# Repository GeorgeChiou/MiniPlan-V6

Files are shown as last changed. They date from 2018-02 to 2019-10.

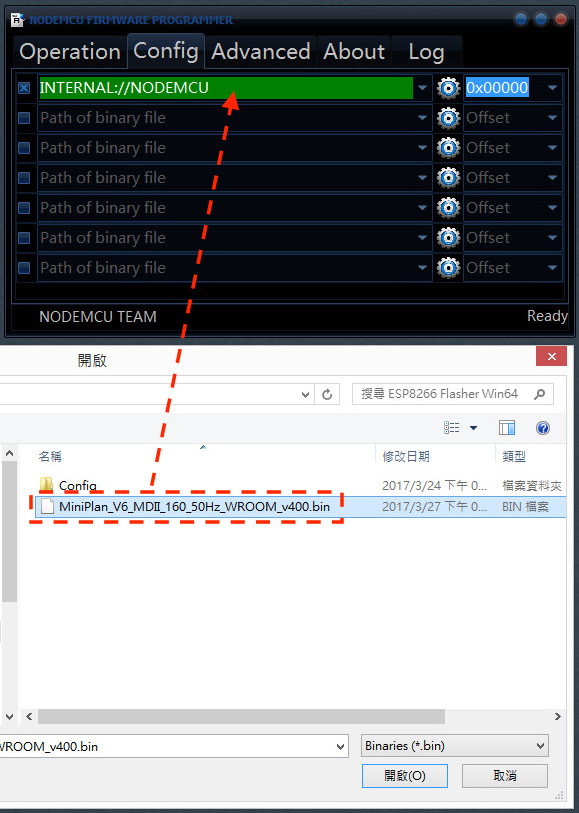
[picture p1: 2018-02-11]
ESP8266 Flasher Win32/Step3.jpg

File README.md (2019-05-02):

# MiniPlan V670 and Robot Power Package V320

MiniPlan V670 is an ideal piece of work for various types of projects when working with up to 20 Servo Motors.<br>

Specifications and Features<br>
Controls up to 20 servo motors (16PWM + 4 GPIO)<br>
Onboard USB to TTL so a regular USB to MicroUSB cable can be used to program the controller<br>
ESP-WROOM-02 directly from ESPRESSIF for faster, better, and stable connection<br>
4MB Flash memory<br>
Arduino IDE Compatible<br>
i2c connection port<br>
TTL connection port<br>
Dimensions L49mm X W43mm X H11.6mm<br>

Specifications of Robot Power Package V320<br>
8.4V/250mAh of power using 3 cells of Lithium Ion Capacitors<br>
Nominal output of 10C (2.5A) and maximum output of 15C (3.75A).<br>
Higher level safety using Lithium Ion Capacitors<br>
Dimensions L60mm X W43mm X H17.6mm<br>

MiniPlan Motion Editor :<br>
<br>

Assembly Instruction :<br>
<br>

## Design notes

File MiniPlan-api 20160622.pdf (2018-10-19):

1. 動作指定

帶入對應的參數即可做動作，但需要等做完後再執行下個動作

URL
{IP}/controller
變數名稱 | 傳遞方法 | 說明
pm | GET | 1: 向前走 2: 向後走 3: 向左走 4: 向右走 99: 停止
pms | GET | 1: Bow 2: Waving 3: Iron Man 4: Apache 5: Balance 6: Warm-Up

範例
http://192.168.4.1/controller?pm=1http://192.168.4.1/controller?pms=5

2. 裝置控制
直接指定 Servo 或 GPIO 的值

Servo Control
{IP}/controller
變數名稱 | 傳遞方法 | 說明
servo | GET | Servo 的編號
value | GET | 變化的數值

範例
http://192.168.4.1/controller?servo=5&value=20

GPIO Control
{IP}/controller
變數名稱 | 傳遞方法 | 說明
gpio | GET | GPIO 的編號
value | GET | 變化的數值

範例
http://192.168.4.1/controller?gpio=5&value=20

3. 參數設定
設定每個 Servo 校正數值

Setting Control
{IP}/save
變數名稱 | 傳遞方法 | 說明
key | GET | Servo 的編號
value | GET | 設定的數值

範例
http://192.168.4.1/save?key=5&value=20

4. 即時動作
傳入每個 Servo 動作矩陣數值

Online Control
{IP}/online
變數名稱 | 傳遞方法 | 說明
m0～m? | GET | Servo 的數值
t1 | GET | 設定執行時間的數值

範例
http://192.168.4.1/online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

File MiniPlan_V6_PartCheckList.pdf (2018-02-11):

Part No. | Print Settings | Qty.

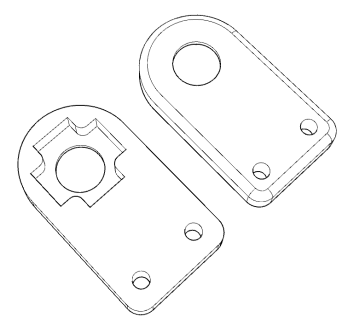
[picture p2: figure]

MiniPlan6_11 | Supports: No Resolution: 0.2mm Infill: 30% | □ 4

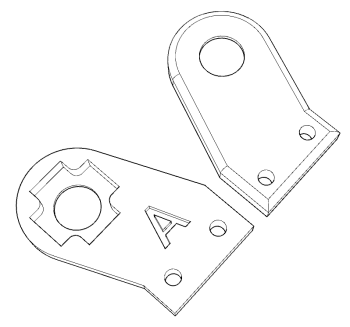
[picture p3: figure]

MiniPlan6_12A | Supports: No Resolution: 0.2mm Infill: 30% | □ 3

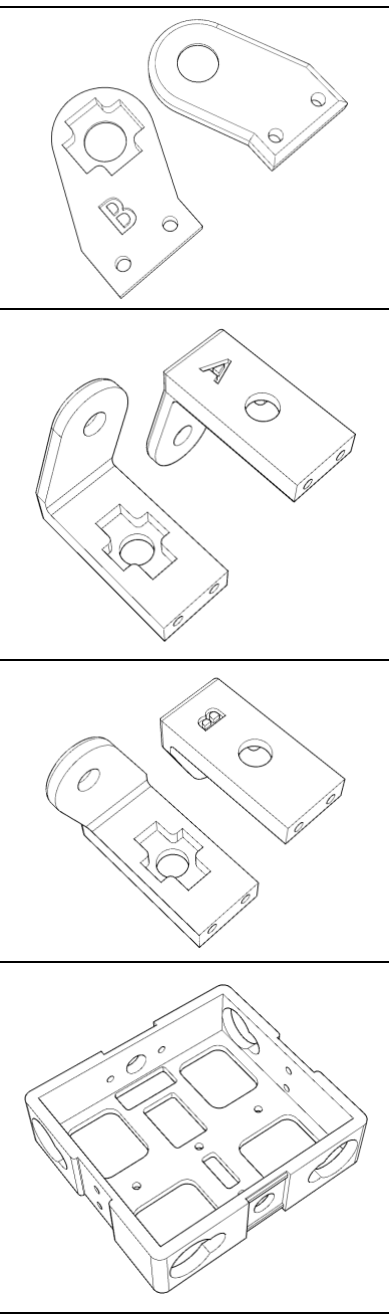
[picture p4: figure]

MiniPlan6_12B | Supports: No Resolution: 0.2mm Infill: 30% | □ 3
MiniPlan6_13A | Supports: No Resolution: 0.2mm Infill: 30% | □ 2
MiniPlan6_13B | Supports: No Resolution: 0.2mm Infill: 30% | □ 2
MiniPlan6_20 | Supports: No Resolution: 0.2mm Infill: 30% | □ 1

Part No. | Print Settings | Qty.

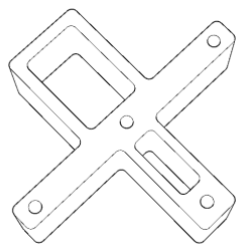
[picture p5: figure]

MiniPlan6_21 | Supports: No Resolution: 0.2mm Infill: 30% | □ 1
MiniPlan6_22B | Supports: No Resolution: 0.2mm Infill: 30% | □ 1

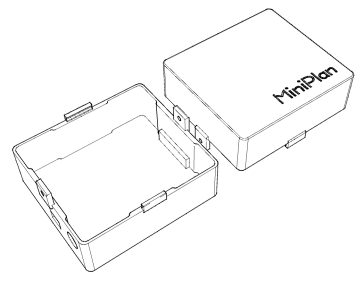
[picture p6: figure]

MiniPlan6_23B | Supports: No Resolution: 0.2mm Infill: 30% | □ 1

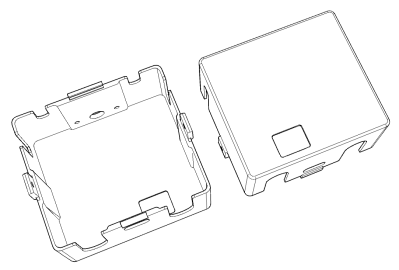
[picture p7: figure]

MiniPlan6_24B | Supports: No Resolution: 0.2mm Infill: 30% | □ 1

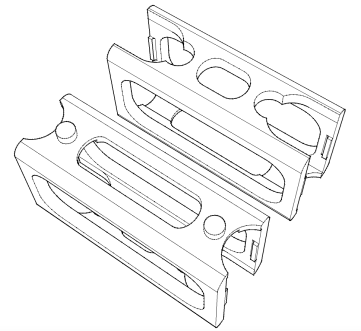
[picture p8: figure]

MiniPlan6_30 | Brim: Yes Supports: No Resolution: 0.2mm Infill: 30% | □ 2
MiniPlan6_31L | Supports: No Resolution: 0.2mm Infill: 20% | □ 1

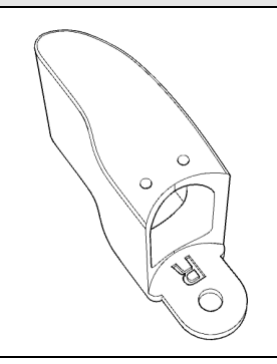
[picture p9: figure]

Part No. | Print Settings | Qty.
MiniPlan6_31R | Supports: No Resolution: 0.2mm Infill: 20% | □ 1

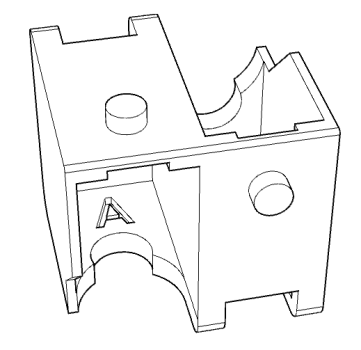
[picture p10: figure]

MiniPlan6_40A | Supports: Yes Resolution: 0.2mm Infill: 30% | □ 1

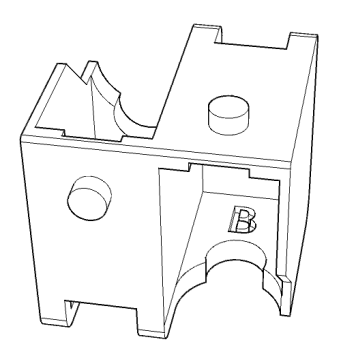
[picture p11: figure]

MiniPlan6_40B | Supports: Yes Resolution: 0.2mm Infill: 30% | □ 1

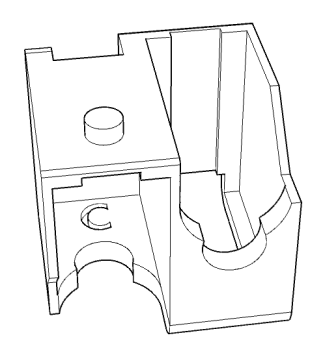
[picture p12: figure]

MiniPlan6_40C | Supports: Yes Resolution: 0.2mm Infill: 30% | □ 1
MiniPlan6_40D | Supports: Yes Resolution: 0.2mm Infill: 30% | □ 1

Part No. | Print Settings | Qty.

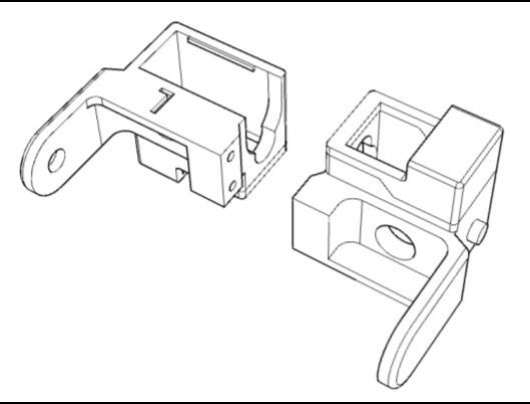
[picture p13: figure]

MiniPlan6_41L | Supports: No Resolution: 0.2mm Infill: 30% | □ 1

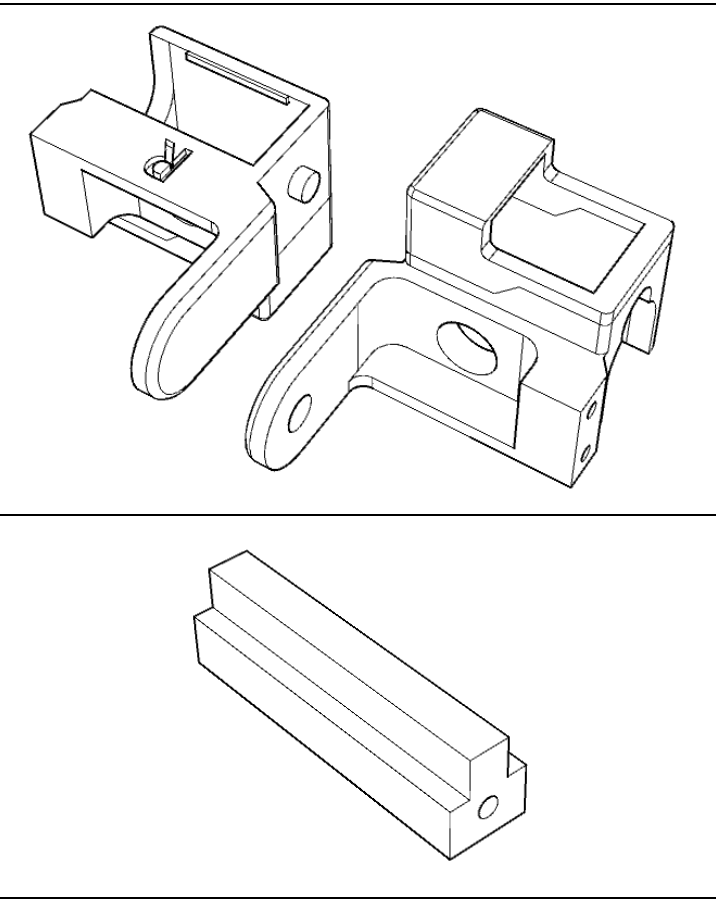
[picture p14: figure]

MiniPlan6_41R | Supports: No Resolution: 0.2mm Infill: 30% | □ 1
MiniPlan6_42 | Supports: No Resolution: 0.2mm Infill: 30% | □ 2

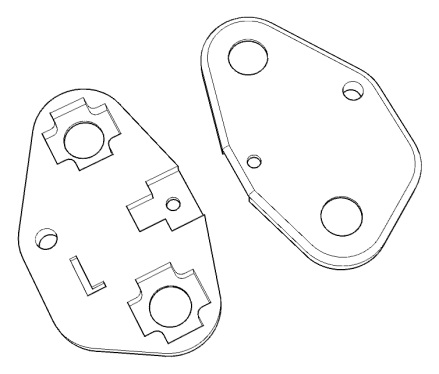
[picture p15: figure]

MiniPlan6_43L | Supports: No Resolution: 0.2mm Infill: 30% | □ 1

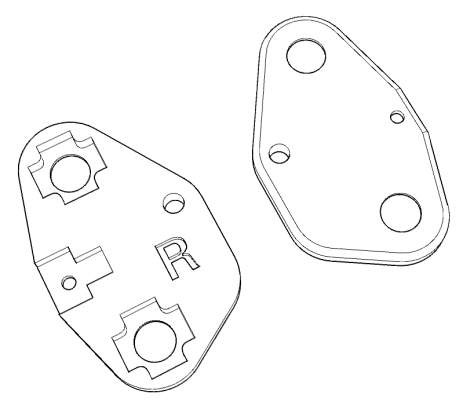
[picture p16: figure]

MiniPlan6_43R | Supports: No Resolution: 0.2mm Infill: 30% | □ 1

Part No. | Print Settings | Qty.

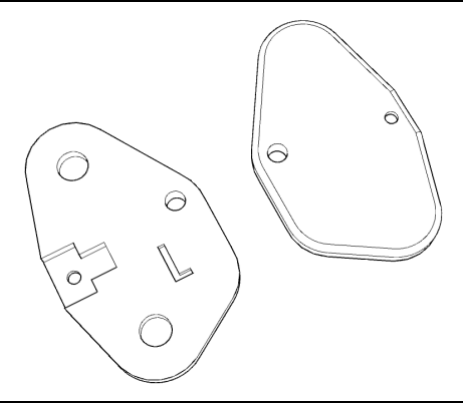
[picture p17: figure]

MiniPlan6_44L | Supports: No Resolution: 0.2mm Infill: 30% | □ 1
MiniPlan6_44R | Supports: No Resolution: 0.2mm Infill: 30% | □ 1
MiniPlan6_45L | Supports: No Resolution: 0.2mm Infill: 30% | □ 1
MiniPlan6_45R | Supports: No Resolution: 0.2mm Infill: 30% | □ 1

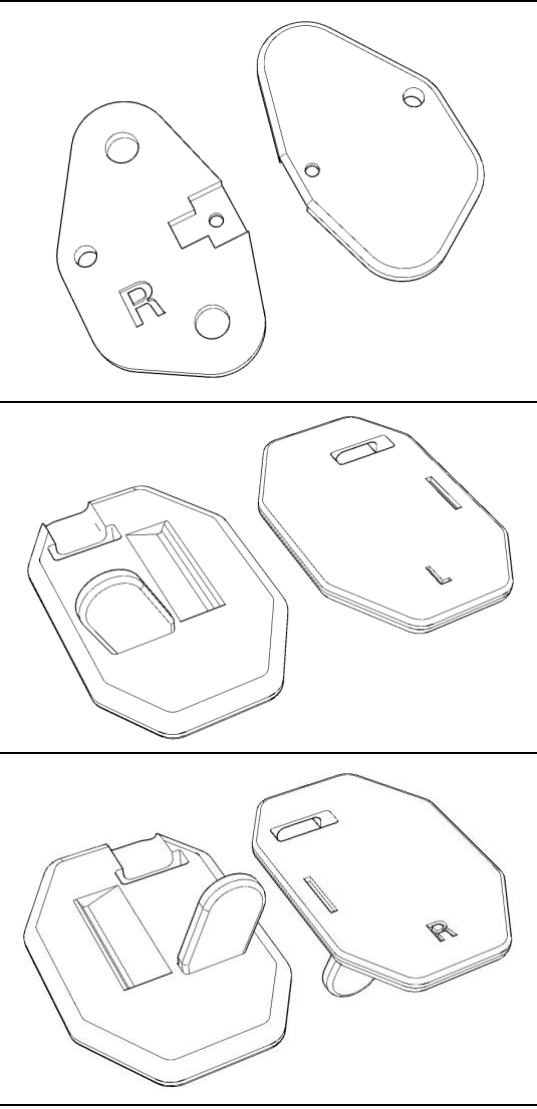
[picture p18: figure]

Print Check & Servo Cut Tool | Part No. | Print Settings | Qty.

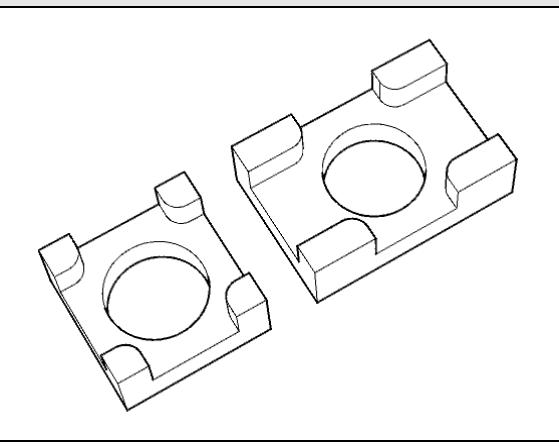
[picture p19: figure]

| MiniPlan6_70 | Supports: No Resolution: 0.2mm Infill: 100% | □ 1

Neck Mode 1 (Fix) | Part No. | Print Settings | Qty.
| MiniPlan6_50 | Supports: No Resolution: 0.2mm Infill: 100% | □ 1
Neck Mode 2 (Can Move) | Part No. | Print Settings | Qty.

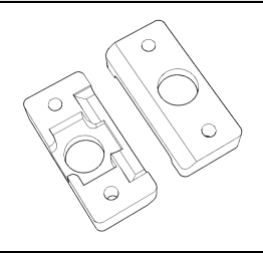
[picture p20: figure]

| MiniPlan6_51 | Supports: No Resolution: 0.2mm Infill: 100% | □ 1
| MiniPlan5_43 | Supports: No Resolution: 0.2mm Infill: 30% | □ 1

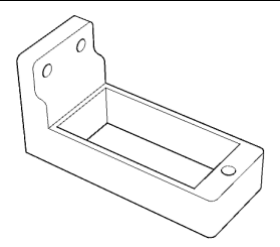
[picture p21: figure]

Skateboard | Part No. | Print Settings | Qty.

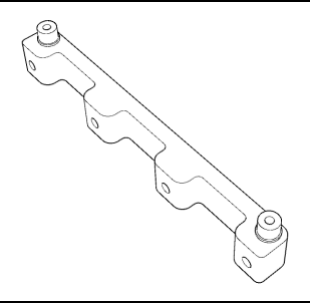
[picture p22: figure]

| MiniPlan6_60 | Supports: No Resolution: 0.2mm Infill: 30% | □ 4

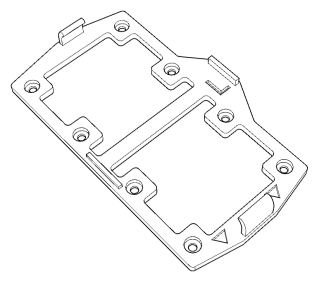
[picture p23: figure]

| MiniPlan6_61L | Supports: No Resolution: 0.2mm Infill: 100% | □ 1
| MiniPlan6_61R | Supports: No Resolution: 0.2mm Infill: 100% | □ 1

Head | Part No. | Print Settings | Qty.

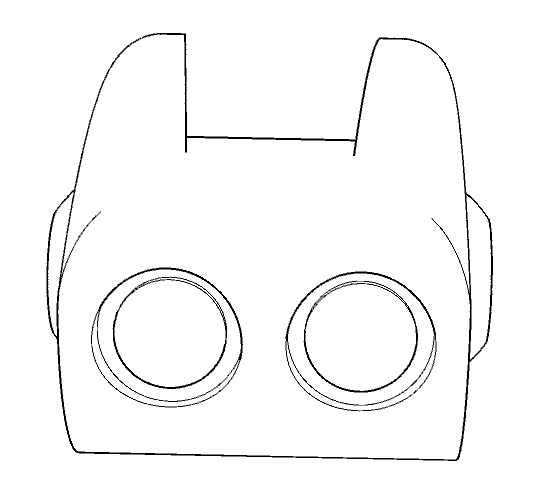
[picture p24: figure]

| MiniPlan5_40 Or MiniPlan5_40_chang | Rafts: Yes Supports: Yes Resolution: 0.2mm Infill: 20% | □ 1

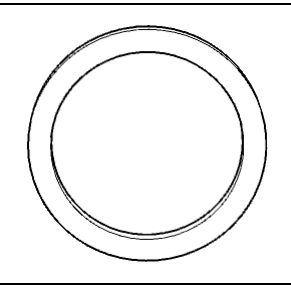
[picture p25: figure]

| MiniPlan51_70 | Supports: No Resolution: 0.2mm Infill: 100% | □ 2

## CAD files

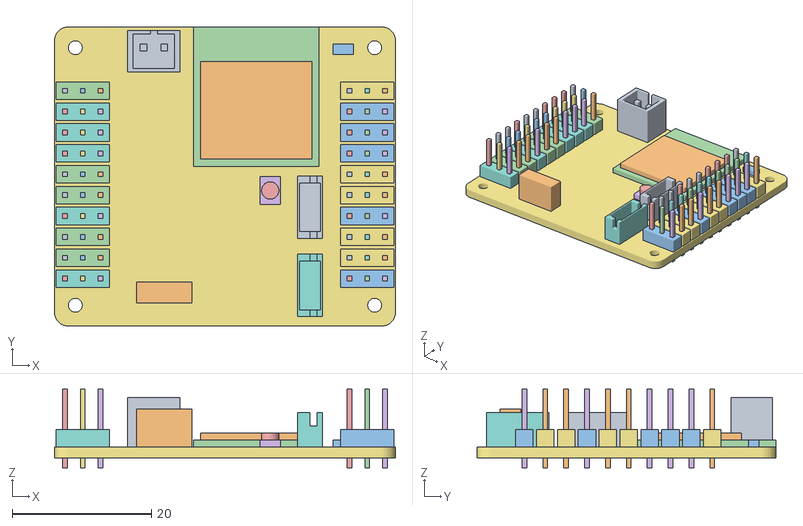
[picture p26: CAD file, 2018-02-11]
3D Mould Part/MiniPlan PCBA PIN v6.7.obj
49.0 x 43.0 x 11.3

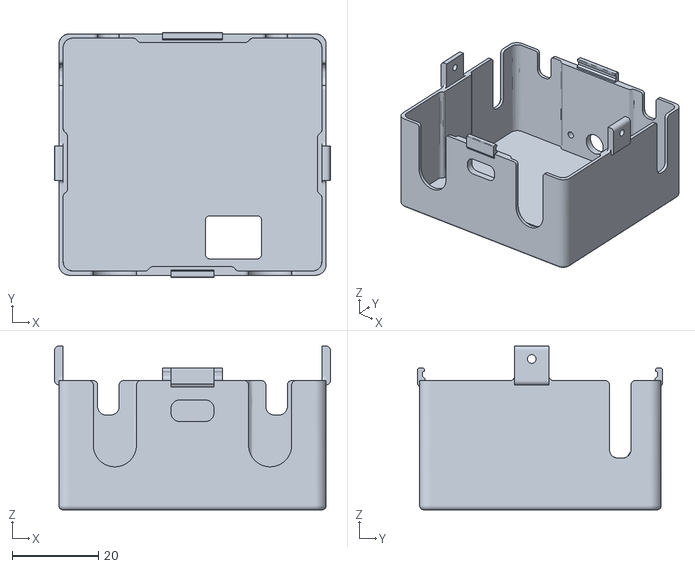
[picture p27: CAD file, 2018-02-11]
3D Mould Part/MiniPlan6_24B.stl
64.0 x 56.8 x 38.0

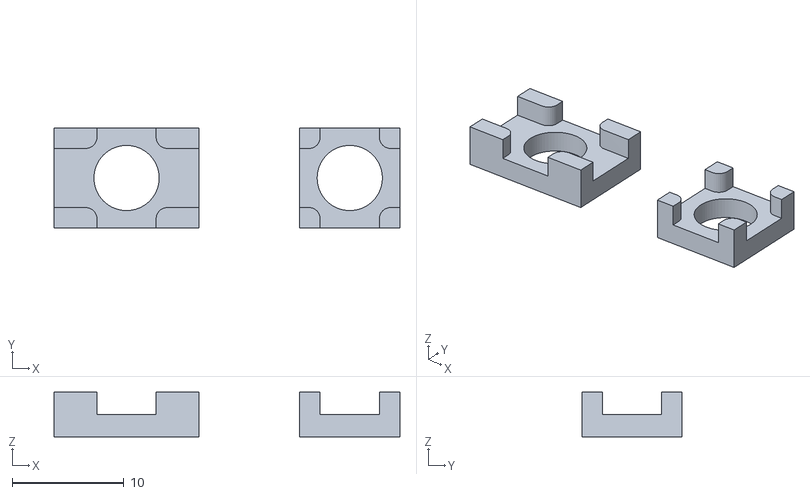
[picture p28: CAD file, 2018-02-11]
3D Mould Part/MiniPlan6_70.stl
31.0 x 9.00 x 4.00

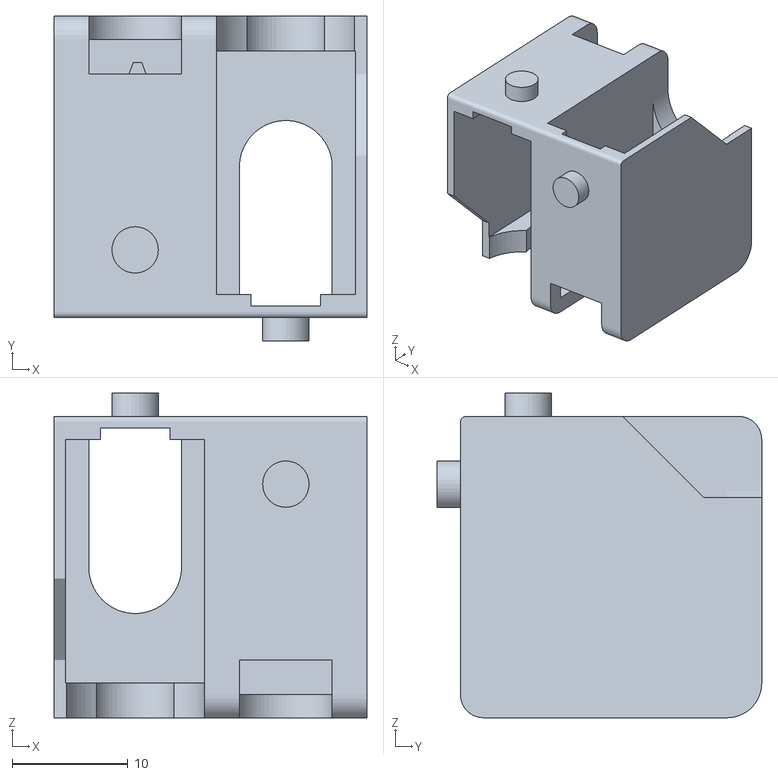
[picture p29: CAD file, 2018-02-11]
3D Mould Part/MiniPlan6_40A.stl
27.0 x 28.0 x 28.0

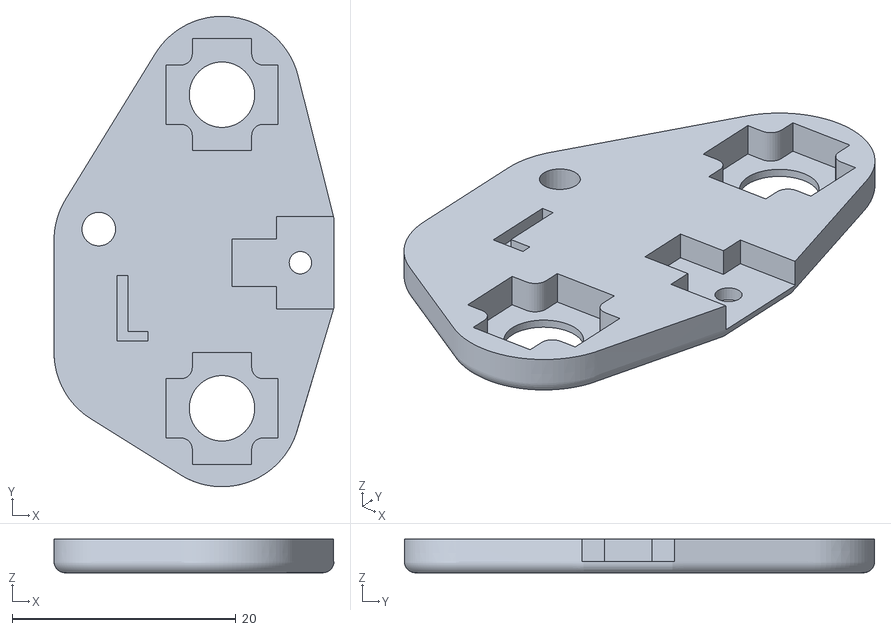
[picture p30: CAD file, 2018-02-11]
3D Mould Part/MiniPlan6_43L.stl
25.0 x 42.0 x 3.00

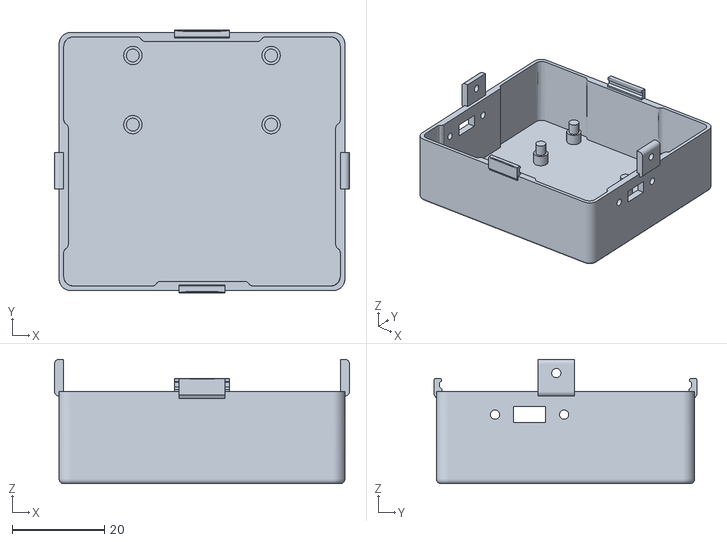
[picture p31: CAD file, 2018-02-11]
3D Mould Part/MiniPlan6_23A.stl
64.0 x 57.0 x 27.0

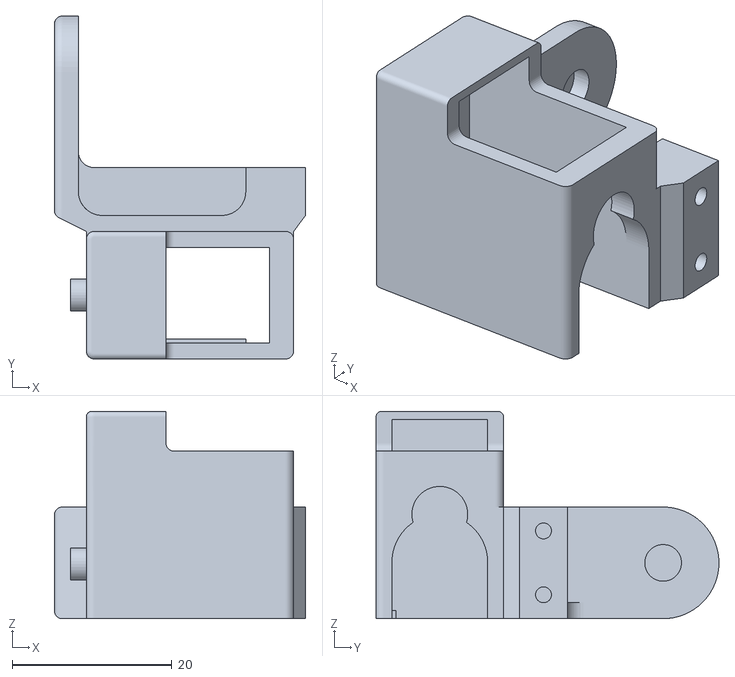
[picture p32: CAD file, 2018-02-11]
3D Mould Part/MiniPlan6_41L.stl
31.5 x 43.0 x 26.0

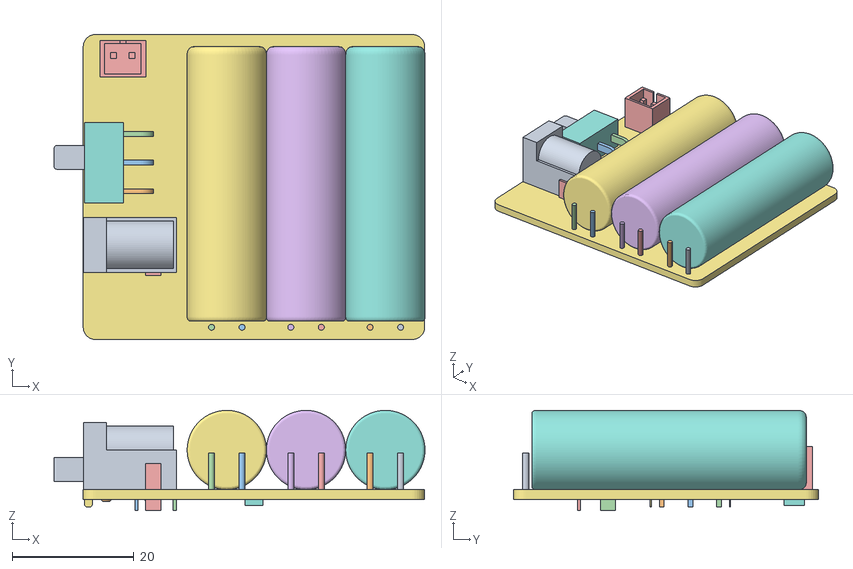
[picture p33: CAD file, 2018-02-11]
3D Mould Part/Robot Power Package V3.2 PCBA.obj
60.8 x 50.0 x 16.4

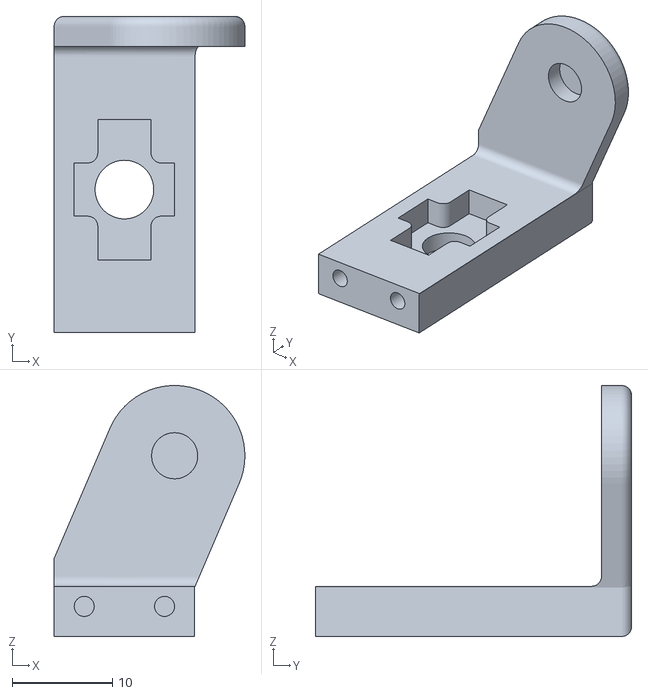
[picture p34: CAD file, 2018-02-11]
3D Mould Part/MiniPlan6_13A.stl
19.0 x 31.5 x 25.0

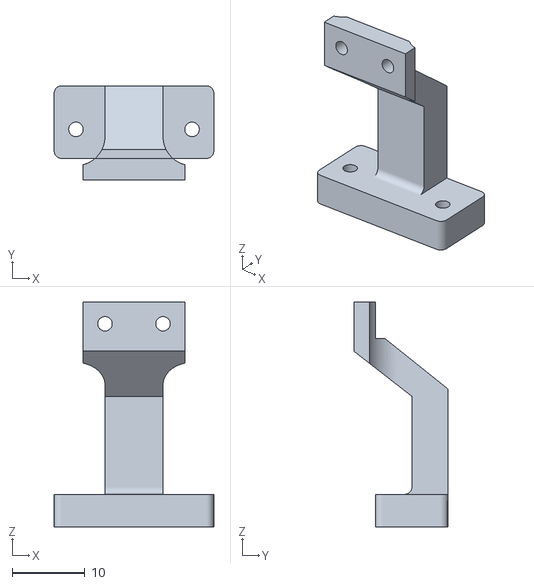
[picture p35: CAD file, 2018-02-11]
3D Mould Part/MiniPlan6_50.stl
22.0 x 13.0 x 31.0

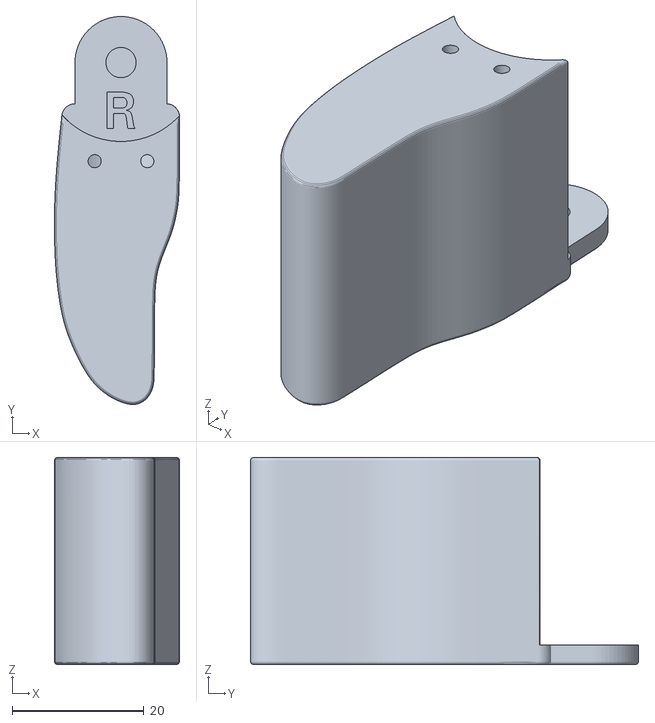
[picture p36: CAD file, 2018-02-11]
3D Mould Part/MiniPlan6_31R.stl
19.0 x 59.0 x 31.5

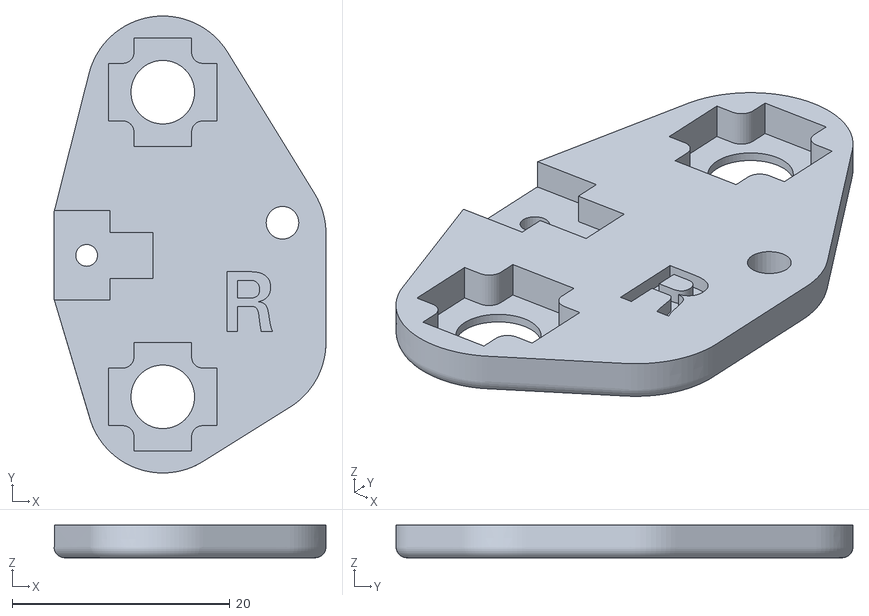
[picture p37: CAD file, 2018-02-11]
3D Mould Part/MiniPlan6_43R.stl
25.0 x 42.0 x 3.00

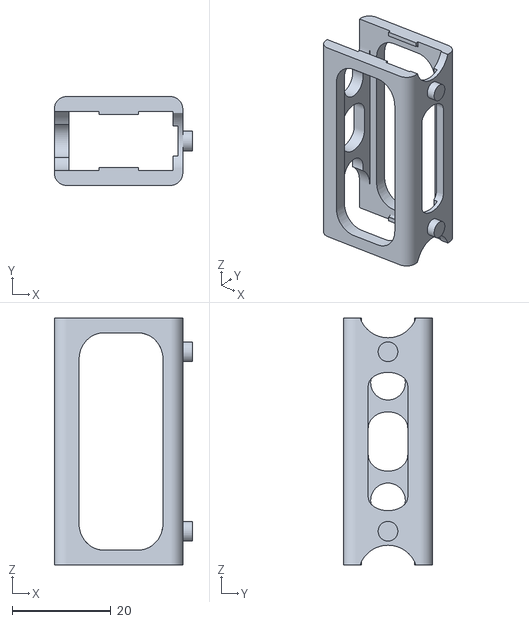
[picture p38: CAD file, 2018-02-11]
3D Mould Part/MiniPlan6_30.stl
28.0 x 18.0 x 50.0

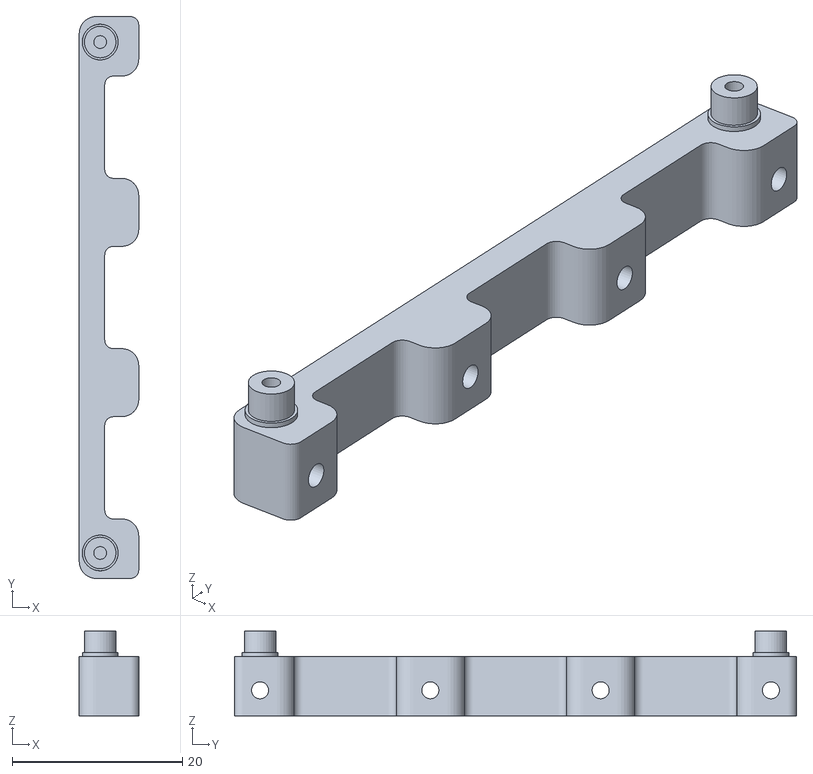
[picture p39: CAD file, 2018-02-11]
3D Mould Part/MiniPlan6_60.stl
7.00 x 66.0 x 9.95

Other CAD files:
3D Mould Part/MiniPlan6_40D.stl
3D Mould Part/MiniPlan6_44R.stl
3D Mould Part/MiniPlan6_40B.stl
3D Mould Part/MiniPlan6_12A.stl
3D Mould Part/MiniPlan51_70.stl
3D Mould Part/MiniPlan5_40.obj
3D Mould Part/MiniPlan5_43.stl
3D Mould Part/MiniPlan6_11.stl
3D Mould Part/MiniPlan6_12B.stl
3D Mould Part/MiniPlan6_13B.stl
3D Mould Part/MiniPlan6_20.stl
3D Mould Part/MiniPlan6_21.stl
3D Mould Part/MiniPlan6_22A.stl
3D Mould Part/MiniPlan6_22B.stl
3D Mould Part/MiniPlan6_23B.stl
3D Mould Part/MiniPlan6_23C.stl
3D Mould Part/MiniPlan6_23_MightyNet.stl
3D Mould Part/MiniPlan6_24A.stl
3D Mould Part/MiniPlan6_31L.stl
3D Mould Part/MiniPlan6_40C.stl
3D Mould Part/MiniPlan6_41R.stl
3D Mould Part/MiniPlan6_42.stl
3D Mould Part/MiniPlan6_44L.stl
3D Mould Part/MiniPlan6_45L.stl
3D Mould Part/MiniPlan6_45R.stl
3D Mould Part/MiniPlan6_51.stl
3D Mould Part/MiniPlan6_61L.stl
3D Mould Part/MiniPlan6_61R.stl

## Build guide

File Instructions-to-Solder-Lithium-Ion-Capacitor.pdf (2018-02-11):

## Instructions to Solder Lithium Ion Capacitor

Robot Power Pack V320

Due to international shipping regulations of Lithium Ion Batteries, although we are using Super Lithium Ion Capacitors on our product, in which classified as a high-volume Super Capacitor, to avoid issues with customs during exporting and importing, we've decided to leave the parts aside so the examiners don't misunderstood the product contained rechargeable batteries of Lithium Ion or NIMH etc..
Please follow the instructions below to properly install and solder these capacitors on to the Robot Power Pack V320 before enjoying the fun of our products!
1. Contents of received package,
1 x Robot Power Package V320 semi-populated board
3 x 2.4V Super Lithium Ion Capacitor (picture shows 250mAh version)

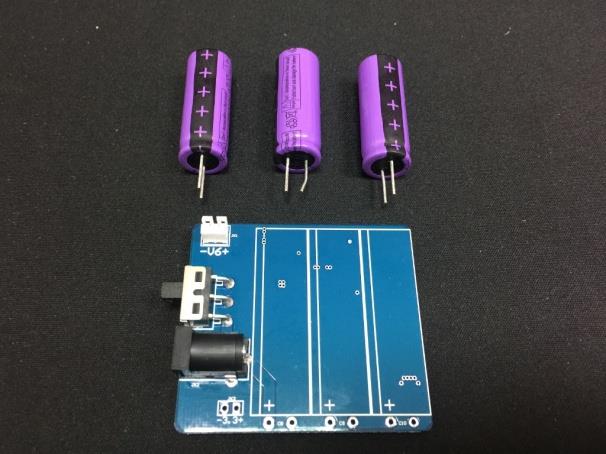
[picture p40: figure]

2. User fingers to bend the leads of capacitor as shown (bend both of them to the same direction). Note: Don't use conductive tools to bend the leads at the same time, shorting the two leads will cause instand discharge in which might damage your tools and the component.

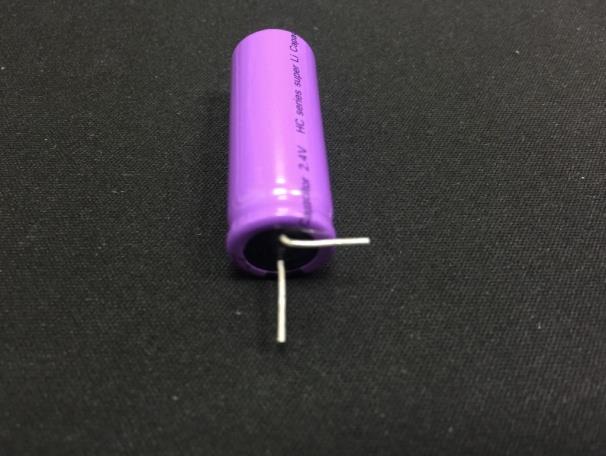
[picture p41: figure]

3. Insert the capacitor with the correct polarity.

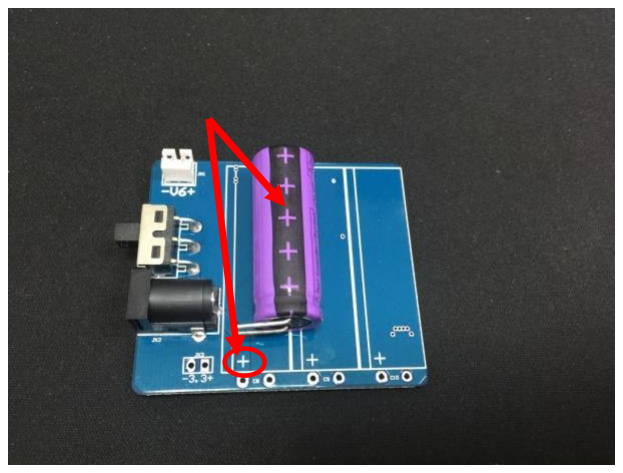
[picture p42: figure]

4. Insert the Capacitor onto the PCB as shown

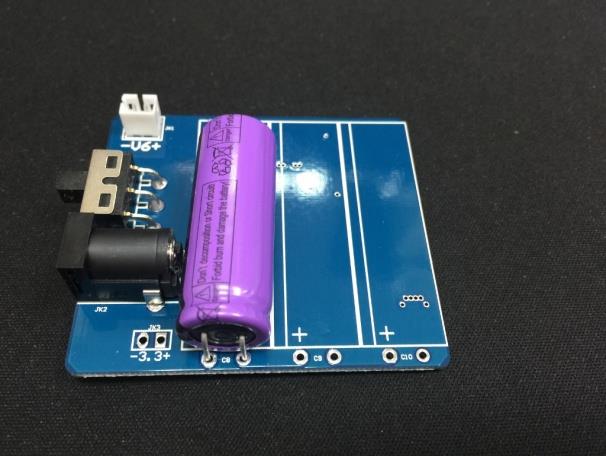
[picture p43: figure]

5. Solder the pins to PCB.
NOTE: Do not head the pins for too long in which may cause damage to components.

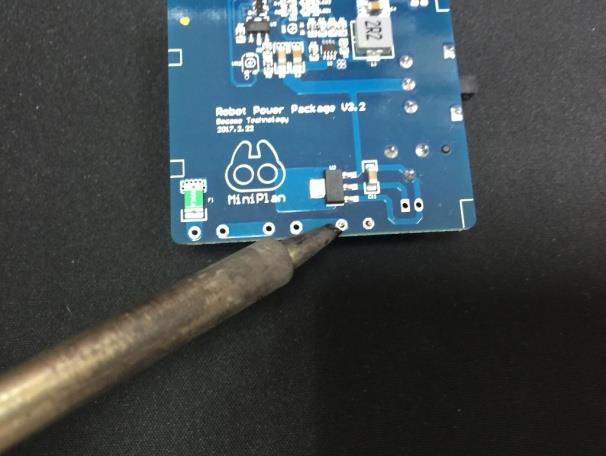
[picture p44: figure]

6. Repeat steps 1~5

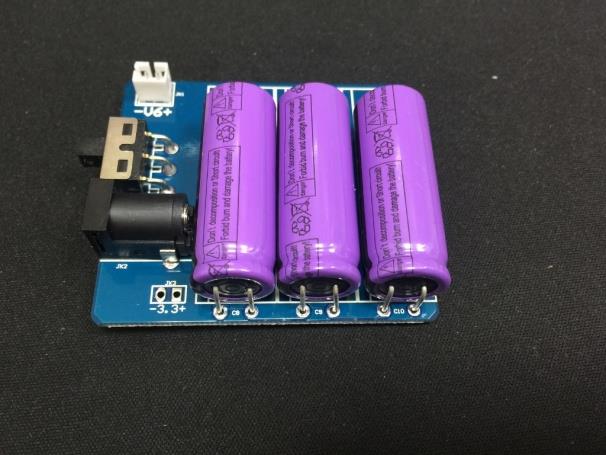
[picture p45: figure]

7. Apply adhesive between tips of capacitor and PCB to minimize movement.

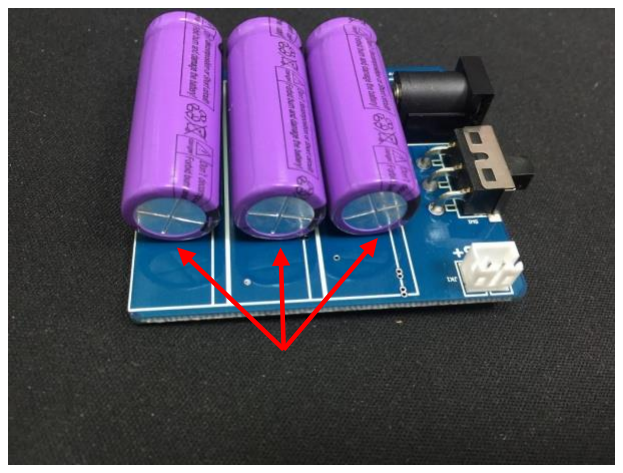
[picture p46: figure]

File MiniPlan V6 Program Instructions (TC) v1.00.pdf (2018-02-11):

# MiniPlan 編寫程式安裝說明

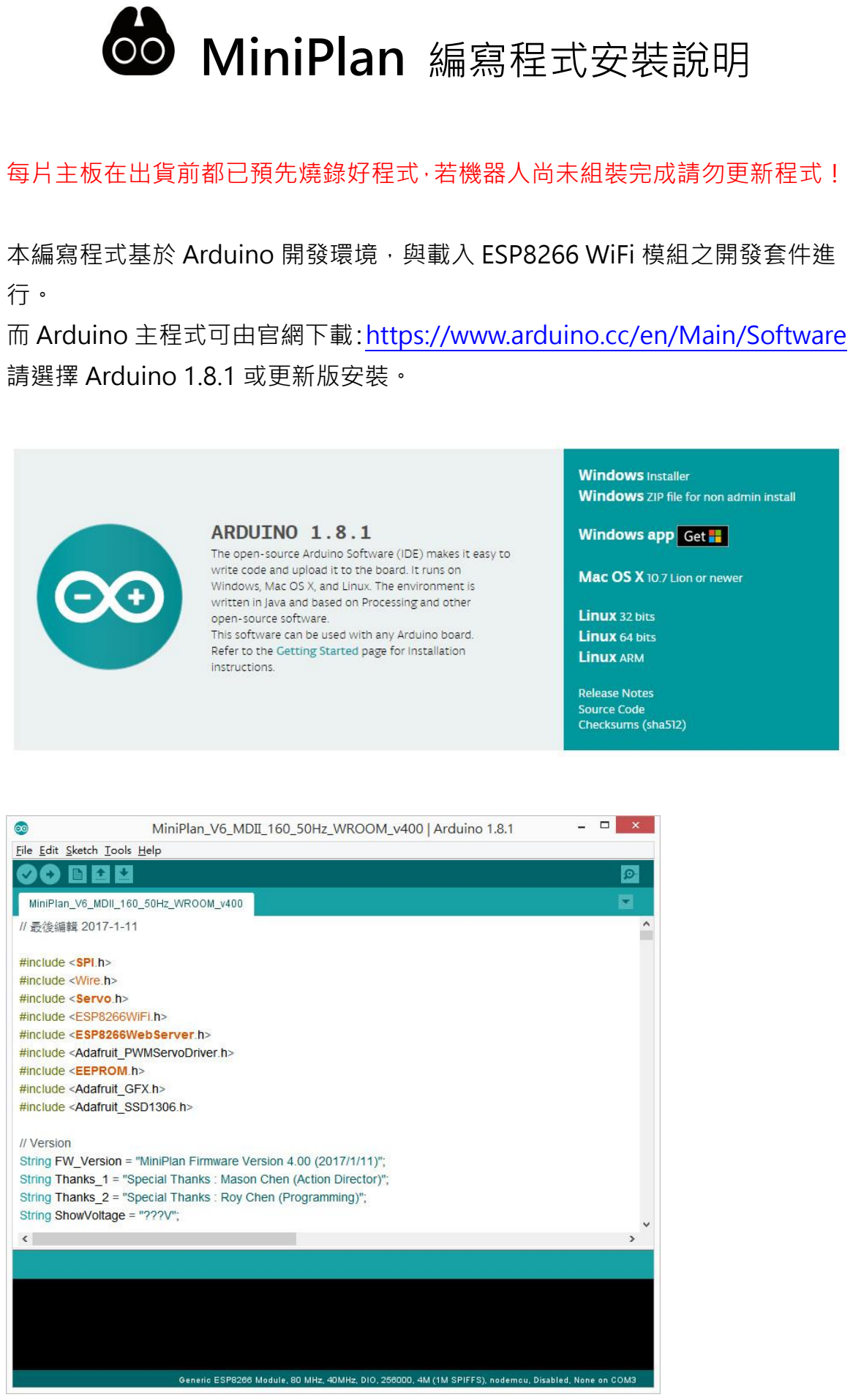
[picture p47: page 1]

每片主板在出貨前都已預先燒錄好程式，若機器人尚未組裝完成請勿更新程式！

本編寫程式基於 Arduino 開發環境，與載入 ESP8266 WiFi 模組之開發套件進 行。
而 Arduino 主程式可由官網下載：https://www.arduino.cc/en/Main/Software 請選擇 Arduino 1.8.1 或更新版安裝。

## 安裝檔案說明：

將下載 Zip 檔案接壓縮後，會有以下檔案。

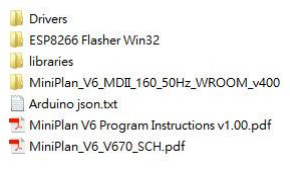
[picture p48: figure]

檔案夾 Drivers 為 USB 連線驅動程式。

檔案夾 ESP8266 Flasher Win32 為韌體燒錄重置或更新程式。

檔案夾 libraries 內的所有檔案
需拷貝到 My Documents\Arduino\Libraries\

檔案夾 MiniPlan_V6_MDII_160_50Hz_WROOM_v400 需拷貝到 My Documents\Arduino\

Arduino json.txt，下載 ESP8266 開發環境網站連結。

PDF 文件：
MiniPlan V6 Program Instructions v1.00.pdf，目前正在閱覽的文件。 MiniPlan_V6_V670_SCH.pdf，主控板電路圖。

## 安裝 ESP8266 WiFi 模組之開發套件：

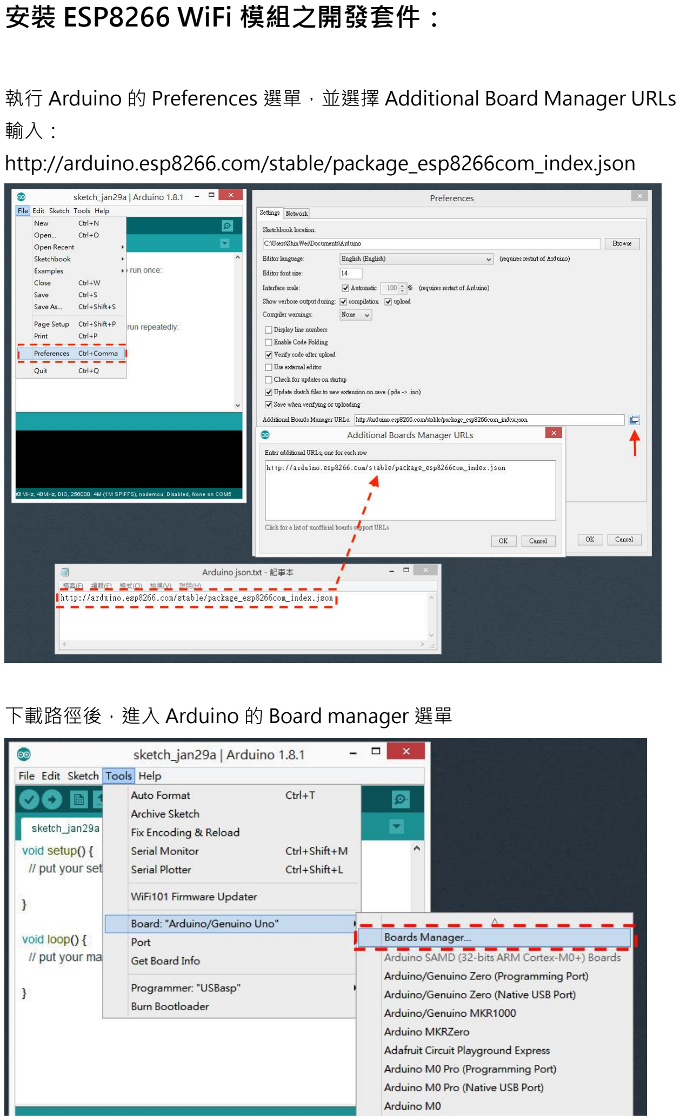
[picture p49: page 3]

執行 Arduino 的 Preferences 選單，並選擇 Additional Board Manager URLs 輸入：
http://arduino.esp8266.com/stable/package_esp8266com_index.json

下載路徑後，進入 Arduino 的 Board manager 選單

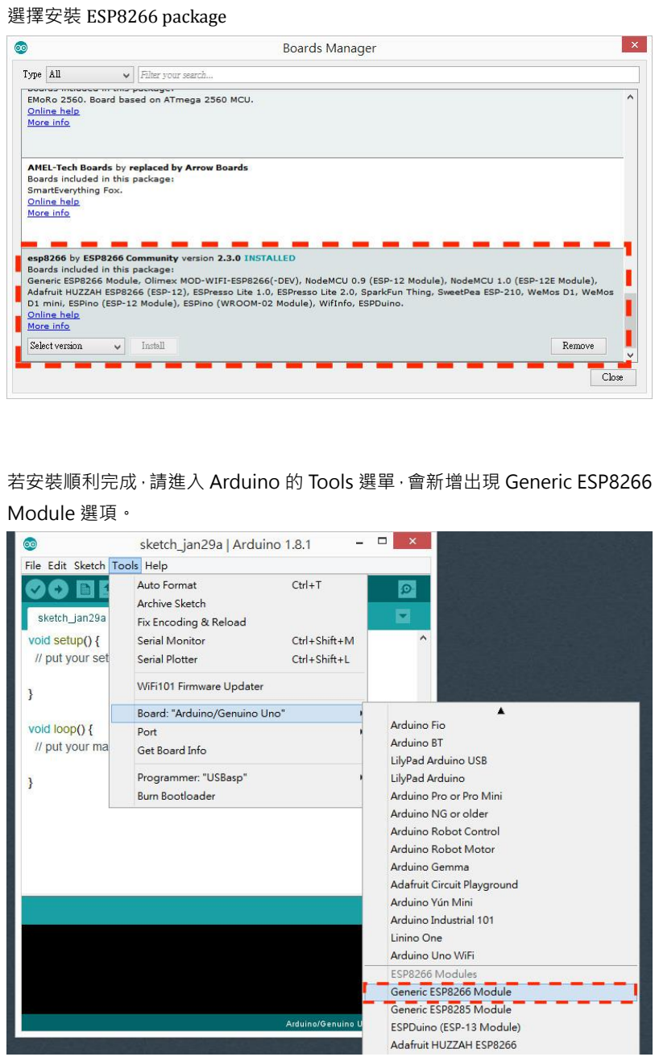
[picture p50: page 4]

選擇安裝 ESP8266 package

若安裝順利完成，請進入 Arduino 的 Tools 選單，會新增出現 Generic ESP8266 Module 選項。

請參照圖面上設定燒錄方式即可。

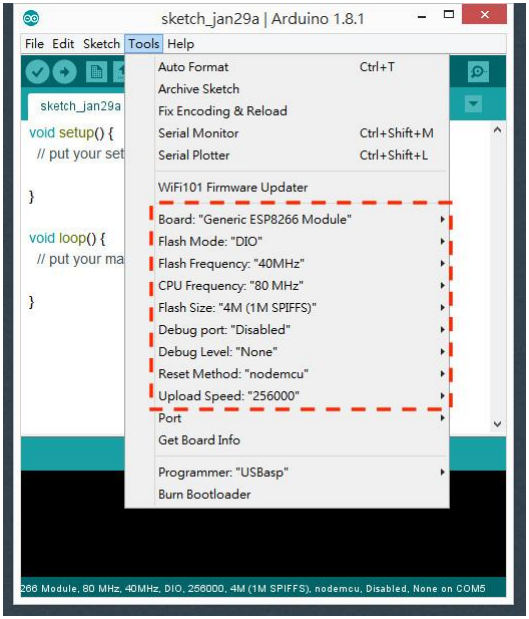
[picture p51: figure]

最後是安裝拷貝 Library。

一般來說都會在 Documents 目錄下找到！

再將解壓縮後的檔案夾 libraries 內的所有檔案拷貝進去即可。

## 安裝 PL2303TA USB to TTL 驅動程式：

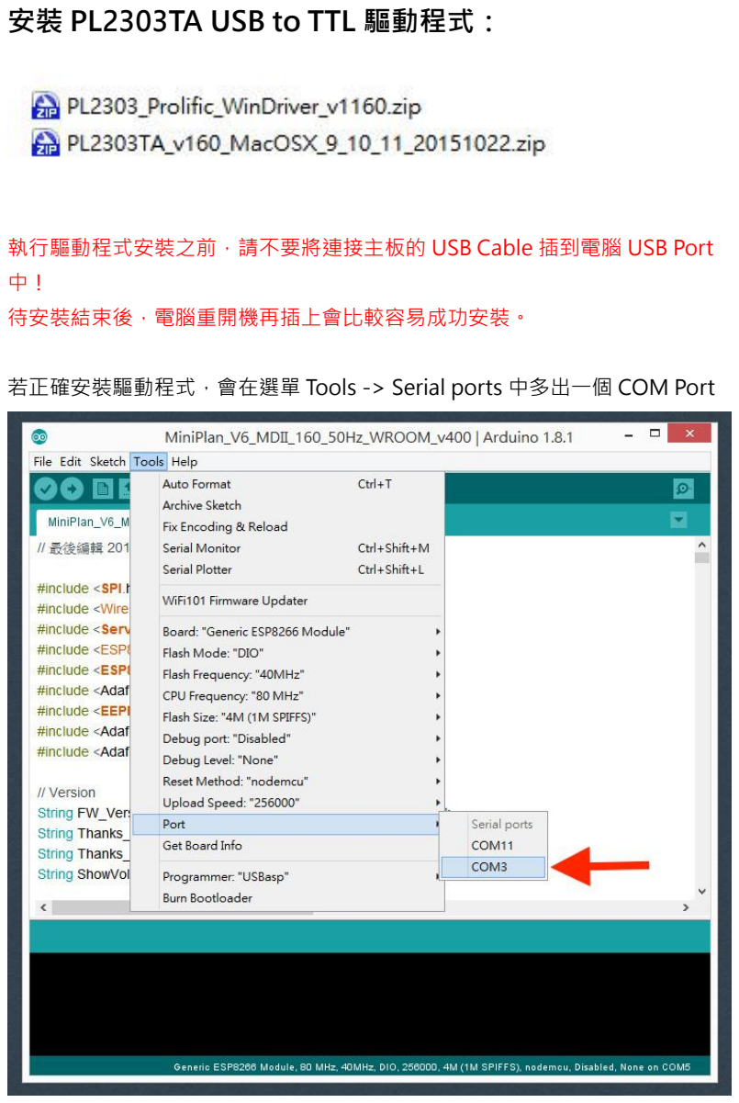
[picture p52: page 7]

執行驅動程式安裝之前，請不要將連接主板的 USB Cable 插到電腦 USB Port 中！
待安裝結束後，電腦重開機再插上會比較容易成功安裝。

若正確安裝驅動程式，會在選單 Tools -> Serial ports 中多出一個 COM Port

## 程式上傳硬體連接設置：

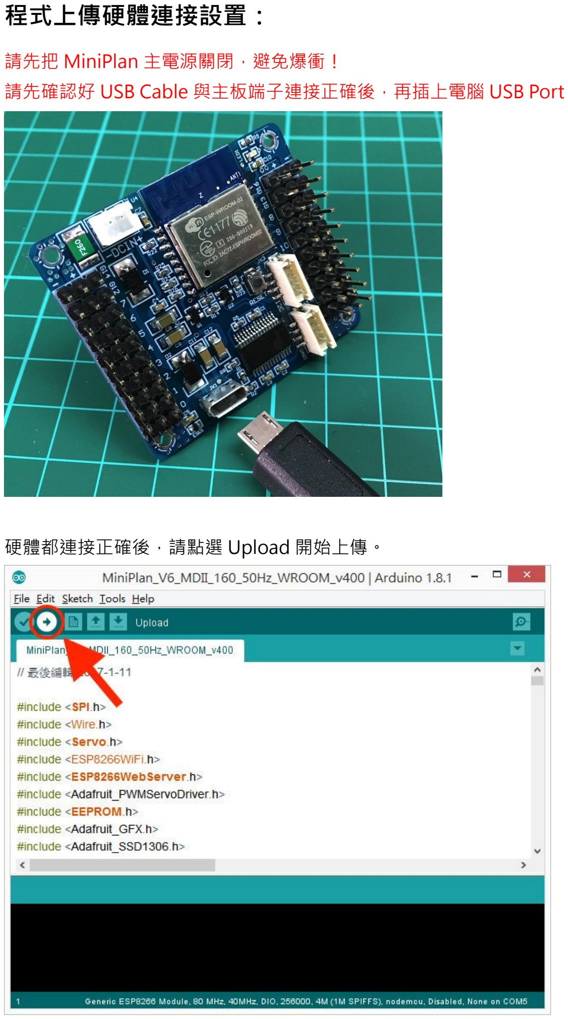
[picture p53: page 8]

請先把 MiniPlan 主電源關閉，避免爆衝！
請先確認好 USB Cable 與主板端子連接正確後，再插上電腦 USB Port

硬體都連接正確後，請點選 Upload 開始上傳。

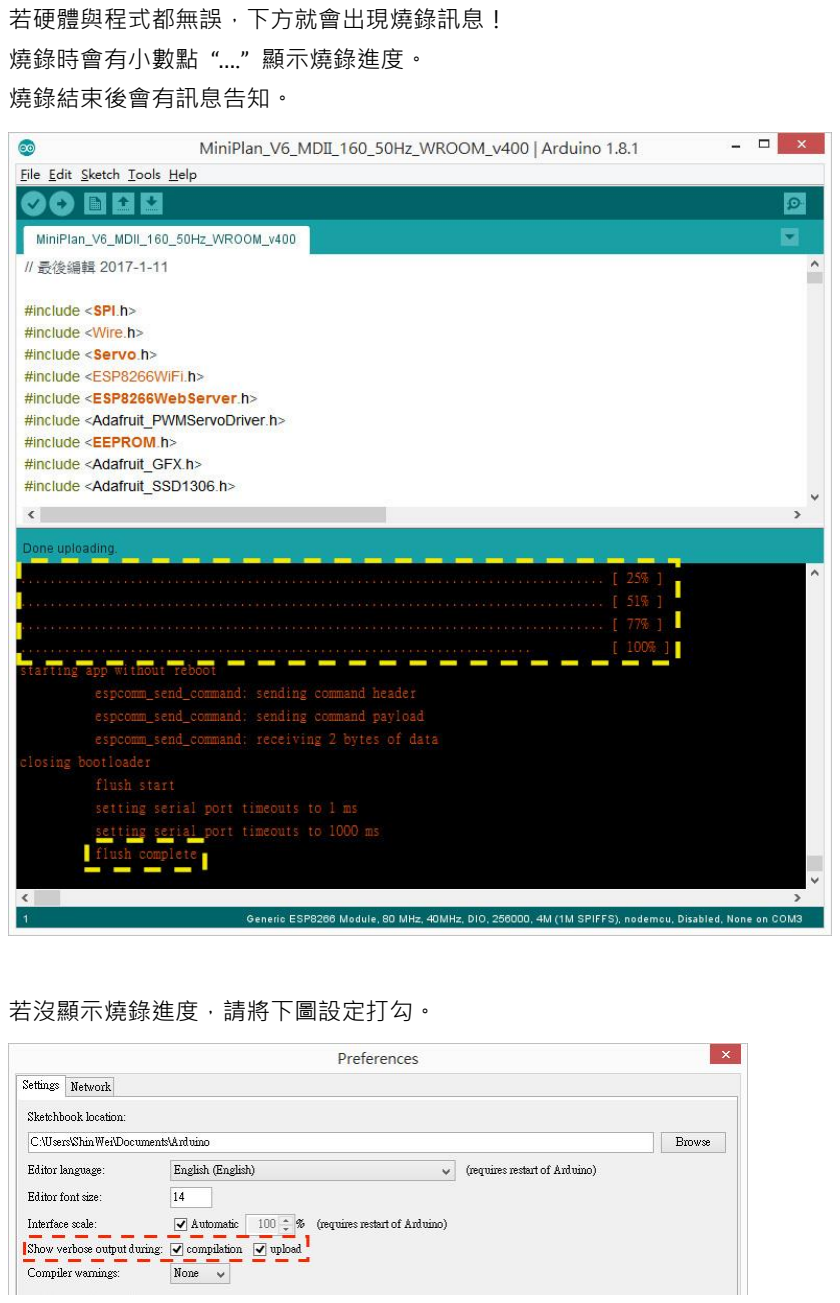
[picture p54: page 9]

若硬體與程式都無誤，下方就會出現燒錄訊息！
燒錄時會有小數點 “….” 顯示燒錄進度。
燒錄結束後會有訊息告知。

若沒顯示燒錄進度，請將下圖設定打勾。

## 發生錯誤情況：

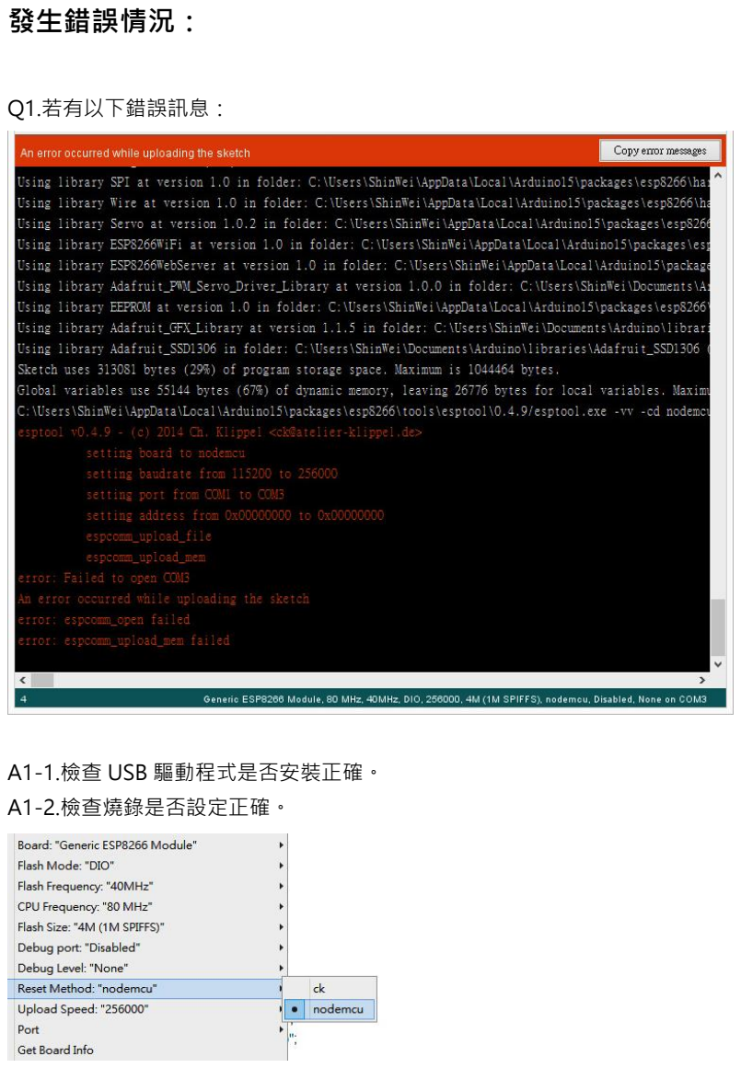
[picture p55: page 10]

Q1.若有以下錯誤訊息：

A1-1.檢查 USB 驅動程式是否安裝正確。
A1-2.檢查燒錄是否設定正確。

Q2.若有以下錯誤訊息：

A2.檢查檔案夾 libraries 內的所有檔案是否安裝正確。

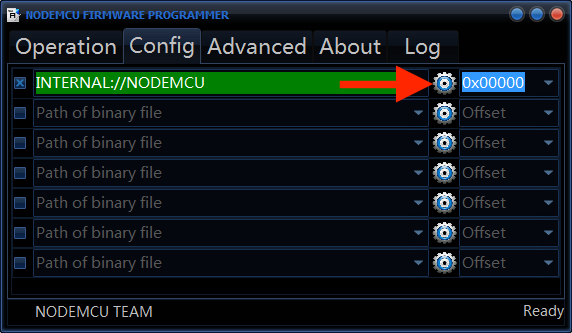
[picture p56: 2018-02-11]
ESP8266 Flasher Win32/Step2.jpg

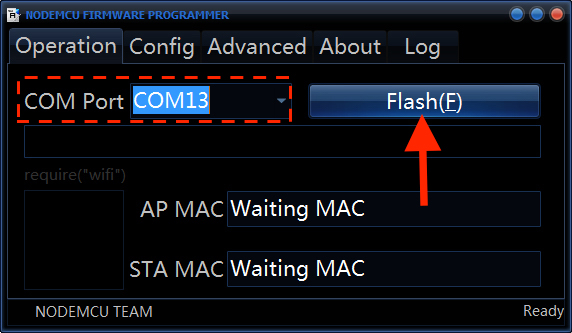
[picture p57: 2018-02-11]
ESP8266 Flasher Win32/Step4.jpg

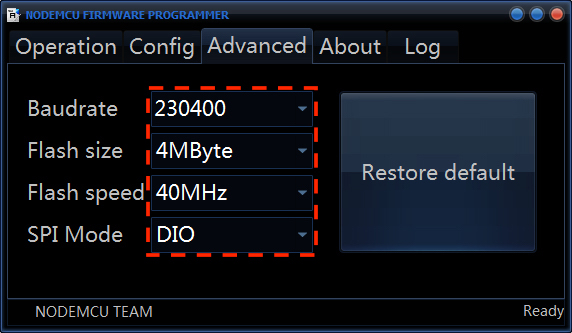
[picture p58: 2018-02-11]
ESP8266 Flasher Win32/Step1.jpg

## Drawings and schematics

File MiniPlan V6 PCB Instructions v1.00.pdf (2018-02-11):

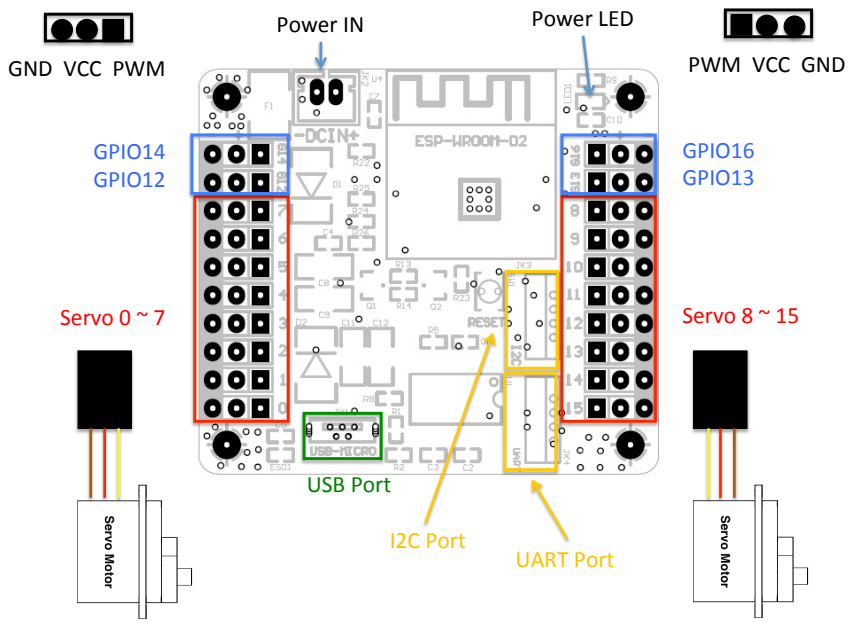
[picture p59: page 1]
Servo 0 ~ 7; Servo 8 ~ 15; GPIO16 GPIO13; GPIO14 GPIO12; USB Port; Power IN; GND VCC PWM; PWM VCC GND; I2C Port; UART Port; Power LED

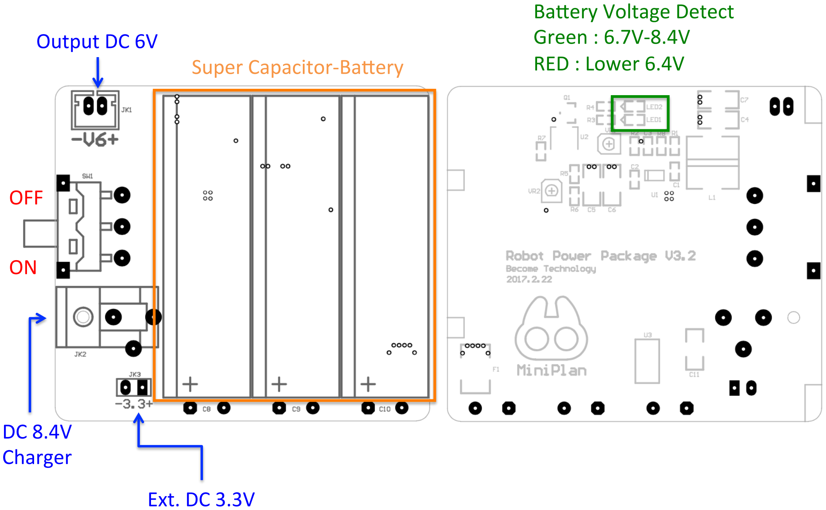
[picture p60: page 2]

OFF

ON

DC 8.4V
Charger
Ext. DC 3.3V

Output DC 6V

BaLery Voltage Detect
Green : 6.7V-8.4V
Super Capacitor-BaLery | RED : Lower 6.4V

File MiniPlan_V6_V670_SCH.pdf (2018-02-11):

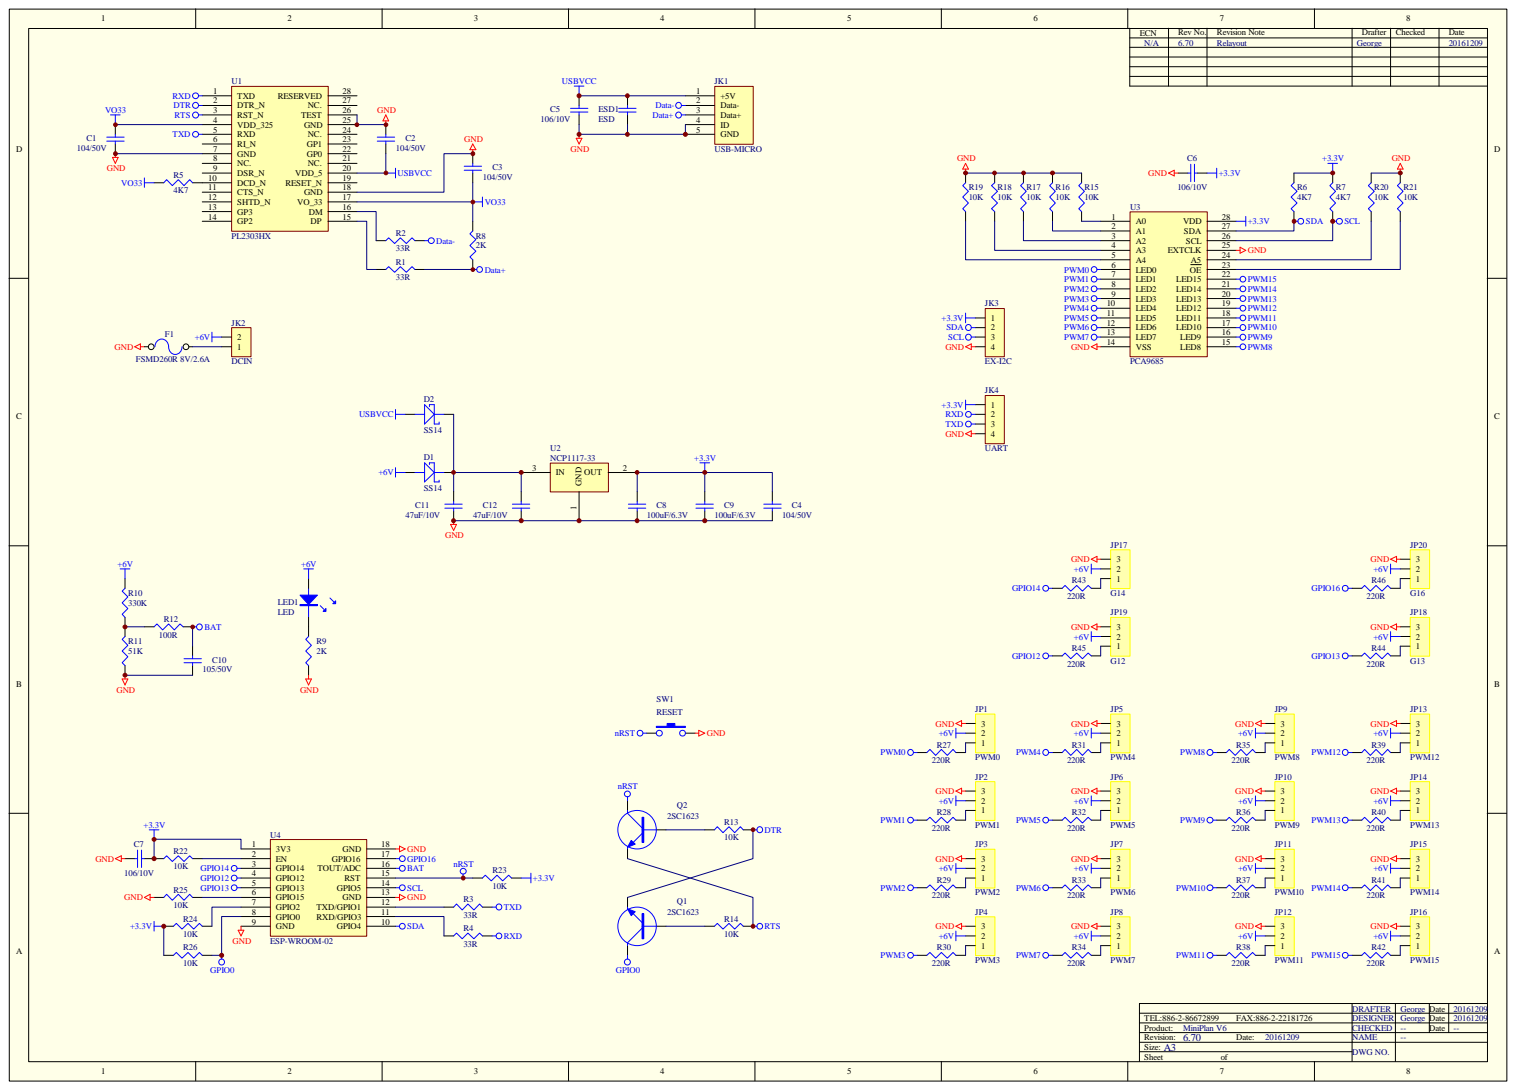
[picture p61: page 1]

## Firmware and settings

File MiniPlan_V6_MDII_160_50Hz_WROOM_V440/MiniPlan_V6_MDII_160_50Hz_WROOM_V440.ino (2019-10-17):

// 最後編輯 2017-3-23
// 初版

// 最後編輯 2017-5-14
// 修正 EEPROM.commit(); 與 EEPROM.h 衝突

// 最後編輯 2017-6-05
// 增加 handleGetEEPROM 傳輸 EEPROM 模式

// 最後編輯 2017-8-28
// 增加網頁對於 中文 支援指令

// 最後編輯 2019-10-17
// 因為 Adafruit_PWM_Servo_Driver_Library 版本問題，改由 Adafruit 正式版本網路下載
// PWM_Frequency = 50;


#include <SPI.h>
#include <Wire.h>
#include <Servo.h>
#include <ESP8266WiFi.h>
#include <ESP8266WebServer.h>
#include <Adafruit_PWMServoDriver.h>
#include <EEPROM.h>
#include <Adafruit_GFX.h>
#include <Adafruit_SSD1306.h>

// Version
String FW_Version = "MiniPlan Firmware Version 4.40 (2019/10/17)";
String Thanks_1 = "Special Thanks : Mason Chen (Action Director)";
String Thanks_2 = "Special Thanks : Roy Chen (Programming)";
String ShowVoltage = "???V";

//  I2C Address 0x3C
#define OLED_RESET LED_BUILTIN
Adafruit_SSD1306 display(-1);

// I2C Address 0x40
Adafruit_PWMServoDriver pwm = Adafruit_PWMServoDriver();

// Servos Matrix
const int ALLMATRIX = 21;    // 0 ~ 15 Servo + GPIO12 + GPIO13 + GPIO14 + GPIO16 + Run Time + Delay Time + PWM Frequency Calibration + Voltage Calibration
const int ALLSERVOS = 20;    // 0 ~ 15 Servo + GPIO12 + GPIO13 + GPIO14 + GPIO16

// ES08MDII Pulse Traveling 700us ~ 2300us 160度
const int PWM_Frequency = 50;    // PWM frequency 50Hz
const int PWMRES_Min = 1;        // PWM Resolution 1
const int PWMRES_Max = 160;      // PWM Resolution 160
const int SERVOMIN = 145;        // 145
const int SERVOMAX = 472;        // 472

// Servo Delay Base Time
const int BASEDELAYTIME = 10;    // 10ms

// AP Password
const char WiFiAPPSK[] = "12345678";

// Voltage Detected
const int Input_Voltage = 795;       // 約 6.00V
const int Input_MinVoltage = 590;    // 約 5.90V 啟動低壓機制
int Voltage_Conter;
int Voltage_Cab = 0;
int Input_Voltage_Low = 0;
int Voltage = Input_Voltage;
int Set_Voltage = Input_Voltage;

// Servo PWM Frequency
int Set_PWM_Freq = PWM_Frequency;

// Motion Data Index
int Servo_PROGRAM;
int Servo_PROGRAM_Stack;

// Servo ID
int GPIO_ID;
int GPIO12_PWM;
int GPIO13_PWM;
int GPIO14_PWM;
int GPIO16_PWM;

// Backup Servo Value
int Running_Servo_POS [ALLMATRIX];

// Engineering model
int Engineering_Model;

// OLED Display Index
int OLED_Display_Index = 0;

// Start Web Server
ESP8266WebServer server(80);

// Start GPIO Software Servo
Servo GPIO12SERVO;
Servo GPIO13SERVO;
Servo GPIO14SERVO;
Servo GPIO16SERVO;



/*============================================================================*/
// ES08MDII - 達文西姿勢
/////////////////////////////////////////////////////    0    ,    1    ,    2    ,    3    ,    4    ,    5    ,    6    ,    7    ,    8    ,    9    ,    10   ,    11   ,    12   ,    13   ,    14   ,    15   ,   G12   ,  G13   ,  G14   ,  G16   ,  ms
int Servo_Act_0 [ ] PROGMEM = {   60,      80,      50,     110,     50,     135,     50,      80,      80,     110,      25,      110,      50,      110,      80,      100,       90,       90,        90,        90,      0  };


/*============================================================================*/
// ES08MDII - 立正
/////////////////////////////////////////////////////    0    ,    1    ,    2    ,    3    ,    4    ,    5    ,    6    ,    7    ,    8    ,    9    ,    10   ,    11   ,    12   ,    13   ,    14   ,    15   ,   G12   ,  G13   ,  G14   ,  G16   ,  ms
int Servo_Act_1 [ ] PROGMEM = {   60,      80,      50,     110,     50,     135,    125,     80,      80,      35,       25,      110,      50,      110,      80,      100,       90,       90,        90,        90,      0  };


/*============================================================================*/
// 鞠躬動作
int Servo_Prg_31_Step = 4;
int Servo_Prg_31 [][ALLMATRIX] PROGMEM = {
  //   0    ,    1    ,    2    ,    3    ,    4    ,    5    ,    6    ,    7    ,    8    ,    9    ,    10   ,    11   ,    12   ,    13   ,    14   ,    15   ,   G12   ,  G13   ,  G14   ,  G16   ,  ms
  {   60,      80,      50,     110,     50,     155,    115,     40,     140,     35,      105,     110,      50,      110,      80,      100,      90,        90,        90,       90,       500   },
  {   60,      65,      50,      60,      50,     155,    115,     40,     140,     35,      105,     110,      97,      110,      95,      100,      90,        90,        90,       90,       500   },
  {   60,      65,      50,      60,      50,     155,    115,     40,     140,     35,      105,     110,      97,      110,      95,      100,      90,        90,        90,       90,       1000 },
  {   60,      80,      50,     110,     50,     135,    125,     80,      80,      35,       25,      110,      50,      110,      80,      100,      90,        90,        90,       90,       800   }   // 立正
};


/*============================================================================*/
// 揮手動作
int Servo_Prg_32_Step = 9;
int Servo_Prg_32 [][ALLMATRIX] PROGMEM = {
  //   0    ,    1    ,    2    ,    3    ,    4    ,    5    ,    6    ,    7    ,    8    ,    9    ,    10   ,    11   ,    12   ,    13   ,    14   ,    15   ,   G12   ,  G13   ,  G14   ,  G16   ,  ms
  {   60,      80,      50,     110,     50,     135,    125,     80,      60,      75,      125,     110,      50,      110,      80,      100,      90,        60,        90,        90,      500  },
  {   60,      80,      50,     110,     50,     135,    125,     80,      80,      35,      125,     110,      50,      110,      80,      100,      90,        60,        90,        90,      300  },
  {   60,      80,      50,     110,     50,     135,    125,     80,      60,      75,      125,     110,      50,      110,      80,      100,      90,        60,        90,        90,      300  },
  {   60,      80,      50,     110,     50,     135,    125,     80,      80,      35,      125,     110,      50,      110,      80,      100,      90,        60,        90,        90,      300  },

  {   60,      80,      50,     110,     50,      35,      85,     100,     80,      35,       30,      110,      50,      110,      80,      100,      90,       120,       90,        90,      500  },
  {   60,      80,      50,     110,     50,      35,     115,     80,      80,      35,       30,      110,      50,      110,      80,      100,      90,       120,       90,        90,      300  },
  {   60,      80,      50,     110,     50,      35,      85,     100,     80,      35,       30,      110,      50,      110,      80,      100,      90,       120,       90,        90,      300  },
  {   60,      80,      50,     110,     50,      35,     115,     80,      80,      35,       30,      110,      50,      110,      80,      100,      90,       120,       90,        90,      300  },

  {   60,      80,      50,     110,     50,     135,    125,     80,      80,      35,       25,      110,      50,      110,      80,      100,      90,        90,        90,        90,      800  }   // 立正
};


/*============================================================================*/
// 鋼鐵人動作
int Servo_Prg_33_Step = 8;
int Servo_Prg_33 [][ALLMATRIX] PROGMEM = {
  //   0    ,    1    ,    2    ,    3    ,    4    ,    5    ,    6    ,    7    ,    8    ,    9    ,    10   ,    11   ,    12   ,    13   ,    14   ,    15   ,   G12   ,  G13   ,  G14   ,  G16   ,  ms
  {   50,      80,      50,     110,     45,     155,    105,    120,     40,     105,      25,      100,      50,      110,      80,       90,       90,        60,        90,        90,      300  },
  {   50,      80,      50,     110,     45,     155,    105,    120,     40,     105,      25,      100,      50,      110,      80,       90,       90,        60,        90,        90,      800  },

  {   70,      80,      50,     110,     60,     135,     55,     120,     40,      55,        5,       115,      50,      110,      80,      110,      90,       120,       90,        90,      300  },
  {   70,      80,      50,     110,     60,     135,     55,     120,     40,      55,        5,       115,      50,      110,      80,      110,      90,       120,       90,        90,      800  },

  {   60,      80,      50,     110,     50,      55,     105,    120,     40,      55,      105,     110,      50,      110,      80,      100,      90,        90,        90,        90,      500  },
  {   60,      65,      50,      95,      50,      55,     140,    120,     40,      15,      105,     110,      65,      110,      94,      100,      90,        90,        90,        90,      500  },

  {   60,      65,      50,      95,      50,      55,     140,    120,     40,      15,      105,     110,      65,      110,      94,      100,      90,        90,        90,        90,      800  },
  {   60,      80,      50,     110,     50,     135,    125,     80,      80,      35,       25,      110,      50,      110,      80,      100,      90,        90,        90,        90,      800  }   // 立正
};


/*============================================================================*/
// 右邊單腳側傾動作
int Servo_Prg_34_Step = 7;
int Servo_Prg_34 [][ALLMATRIX] PROGMEM = {
  //   0    ,    1    ,    2    ,    3    ,    4    ,    5    ,    6    ,    7    ,    8    ,    9    ,    10   ,    11   ,    12   ,    13   ,    14   ,    15   ,   G12   ,  G13   ,  G14   ,  G16   ,  ms
  {   70,      80,      50,     110,     60,     135,    105,     35,      80,      85,       25,      115,      50,      110,      80,      110,      90,        90,        90,        90,      500  },
  {   70,      80,      50,     110,     60,     135,    105,     35,      80,      85,       25,      115,      50,      110,      80,      115,      90,        90,        90,        90,      300  },
  {   70,      80,      50,     110,     60,     135,    105,     35,     140,     15,      105,     100,      50,      110,      80,      120,      90,        90,        90,        90,      500  },
  {   70,      80,      50,     110,     60,     135,    105,     35,     140,     15,      105,     100,      50,      110,      80,      120,      90,       120,       90,        90,      800  },
  {   70,      80,      50,     110,     60,     135,    105,     35,      80,      85,       25,      115,      50,      110,      80,      115,      90,       120,       90,        90,      600  },
  {   70,      80,      50,     110,     60,     135,    105,     35,      80,      85,       25,      115,      50,      110,      80,      110,      90,        90,        90,        90,      500  },
  {   60,      80,      50,     110,     50,     135,    125,     80,      80,      35,       25,      110,      50,      110,      80,      100,      90,        90,        90,        90,      800  }   // 立正
};


/*============================================================================*/
// 左邊單腳平衡動作
int Servo_Prg_35_Step = 12;
int Servo_Prg_35 [][ALLMATRIX] PROGMEM = {
  //   0    ,    1    ,    2    ,    3    ,    4    ,    5    ,    6    ,    7    ,    8    ,    9    ,    10   ,    11   ,    12   ,    13   ,    14   ,    15   ,   G12   ,  G13   ,  G14   ,  G16   ,  ms
  {   50,      80,      50,     110,     45,     135,     50,      80,      80,     110,      25,      100,      50,      110,      80,       90,       90,        90,        90,        90,      500  },
  {   50,      80,      50,     110,     45,      85,      50,      80,      80,     110,      75,      100,      50,      110,      85,       90,       90,        90,        90,        90,      300  },
  {   45,      80,      50,     110,     60,      85,      50,      80,      80,     110,      75,      100,      50,      110,      85,       90,       90,        90,        90,        90,      500  },
  {   45,      80,      50,     110,     60,      85,      50,      80,      80,     110,      75,      100,      50,      110,      85,       90,       90,        90,        90,        90,      600  },

  {   45,      60,      50,      50,      60,      85,      50,      80,      80,     110,      75,      100,      50,      110,      85,       90,       90,        90,        90,        90,      900  },
  {   45,      60,      50,      50,      60,      85,      30,      80,      80,     130,      75,      100,      50,      110,      85,       90,       90,        60,        90,        90,      500  },
  {   45,      60,      50,      50,      60,      85,      70,      80,      80,      90,       75,      100,      50,      110,      85,       90,       90,       120,       90,        90,      500  },
  {   45,      60,      50,      50,      60,      85,      30,      80,      80,     130,      75,      100,      50,      110,      85,       90,       90,        60,        90,        90,      500  },
  {   45,      60,      50,      50,      60,      85,      70,      80,      80,      90,       75,      100,      50,      110,      85,       90,       90,       120,       90,        90,      500  },
  {   45,      60,      50,      50,      60,      85,      50,      80,      80,     110,      75,      100,      50,      110,      85,       90,       90,        90,        90,        90,      500  },
  {   45,      80,      50,     110,     60,      85,      50,      80,      80,     110,      75,      100,      50,      110,      85,       90,       90,        90,        90,        90,      800  },

  {   60,      80,      50,     110,     50,     135,    125,     80,      80,      35,       25,      110,      50,      110,      80,      100,      90,        90,        90,        90,      800  }   // 立正
};
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
void loop(void) {

  // 網頁建構
  server.handleClient();


  // 基本動作
  if (Servo_PROGRAM >= 1 && Input_Voltage_Low == 0 )
  {

    Serial.print("Servo_PROGRAM = ");
    Serial.println(Servo_PROGRAM);

    OLED_Display_Index = OLED_Display_Index + 8;
    if (OLED_Display_Index > 56) {
      OLED_Display_Index = 0;
      display.clearDisplay();
    }
    display.setCursor(0, OLED_Display_Index);
    display.print("Servo_PROGRAM = ");
    display.println(Servo_PROGRAM);
    display.display();

    switch (Servo_PROGRAM)
    {
      case 1:  // 前進
        Servo_PROGRAM_Run(Servo_Prg_1, Servo_Prg_1_Step);
        Servo_PROGRAM_Center();
        break;
      case 2:  // 後退
        Servo_PROGRAM_Run(Servo_Prg_2, Servo_Prg_2_Step);
        Servo_PROGRAM_Center();
        break;
      case 3:  // 左轉
        Servo_PROGRAM_Run(Servo_Prg_3, Servo_Prg_3_Step);
        Servo_PROGRAM_Center();
        break;
      case 4:  // 右轉
        Servo_PROGRAM_Run(Servo_Prg_4, Servo_Prg_4_Step);
        Servo_PROGRAM_Center();
        break;
      case 5:  // 左橫移動作
        Servo_PROGRAM_Run(Servo_Prg_5, Servo_Prg_5_Step);
        Servo_PROGRAM_Center();
        break;
      case 6:  // 右橫移動作
        Servo_PROGRAM_Run(Servo_Prg_6, Servo_Prg_6_Step);
        Servo_PROGRAM_Center();
        break;
      case 7:  // 左踢
        Servo_PROGRAM_Run(Servo_Prg_7, Servo_Prg_7_Step);
        Servo_PROGRAM_Center();
        break;
      case 8:  // 右踢
        Servo_PROGRAM_Run(Servo_Prg_8, Servo_Prg_8_Step);
        Servo_PROGRAM_Center();
        break;
      case 9:  // 向前滑行
        Servo_PROGRAM_Run(Servo_Prg_9, Servo_Prg_9_Step);
        Servo_PROGRAM_Center();
        break;
      case 10: // 向後滑行
        Servo_PROGRAM_Run(Servo_Prg_10, Servo_Prg_10_Step);
        Servo_PROGRAM_Center();
        break;
      case 11: // 面朝上起立
        Servo_PROGRAM_Run(Servo_Prg_11, Servo_Prg_11_Step);
        Servo_PROGRAM_Center();
        break;
      case 12: // 面朝下起立
        Servo_PROGRAM_Run(Servo_Prg_12, Servo_Prg_12_Step);
        Servo_PROGRAM_Run(Servo_Prg_39_3, Servo_Prg_39_3_Step);
        Servo_PROGRAM_Center();
        break;
      case 99: // 待機
        Servo_PROGRAM_Center();
        delay(300);
        break;
      case 100:  // 達文西姿勢
        Servo_PROGRAM_Zero();
        delay(300);
        break;
    }
    Servo_PROGRAM = 0;
  }


  // 動作集
  if (Servo_PROGRAM_Stack >= 1 && Input_Voltage_Low == 0 )
  {

    Serial.print("Servo_PRGRAM_Stack = ");
    Serial.println(Servo_PROGRAM_Stack);

    OLED_Display_Index = OLED_Display_Index + 8;
    if (OLED_Display_Index > 56) {
      OLED_Display_Index = 0;
      display.clearDisplay();
    }
    display.setCursor(0, OLED_Display_Index);
    display.print("Servo_PRG_Stack = ");
    display.println(Servo_PROGRAM_Stack);
    display.display();

    switch (Servo_PROGRAM_Stack)
    {
      case 1:  // 鞠躬動作
        Servo_PROGRAM_Run(Servo_Prg_31, Servo_Prg_31_Step);
        Servo_PROGRAM_Center();
        break;
      case 2:  // 揮手動作
        Servo_PROGRAM_Run(Servo_Prg_32, Servo_Prg_32_Step);
        Servo_PROGRAM_Center();
        break;
      case 3:  // 鋼鐵人動作
        Servo_PROGRAM_Run(Servo_Prg_33, Servo_Prg_33_Step);
        Servo_PROGRAM_Center();
        break;
      case 4:  // 右邊單腳側傾動作
        Servo_PROGRAM_Run(Servo_Prg_34, Servo_Prg_34_Step);
        Servo_PROGRAM_Center();
        break;
      case 5:  // 左邊單腳平衡動作
        Servo_PROGRAM_Run(Servo_Prg_35, Servo_Prg_35_Step);
        Servo_PROGRAM_Center();
        break;
      case 6:  // 暖身動作
        Servo_PROGRAM_Run(Servo_Prg_36, Servo_Prg_36_Step);
        Servo_PROGRAM_Center();
        break;
      case 7:  // 拍手動作
        Servo_PROGRAM_Run(Servo_Prg_37, Servo_Prg_37_Step);
        Servo_PROGRAM_Center();
        break;
      case 8:  // 妖怪手錶動作
        Servo_PROGRAM_Run(Servo_Prg_38, Servo_Prg_38_Step);
        Servo_PROGRAM_Center();
        break;
      case 9:  // 伏地挺身動作
        Servo_PROGRAM_Run(Servo_Prg_39_1, Servo_Prg_39_1_Step);
        Servo_PROGRAM_Run(Servo_Prg_39_2, Servo_Prg_39_2_Step);
        Servo_PROGRAM_Run(Servo_Prg_39_2, Servo_Prg_39_2_Step);
        Servo_PROGRAM_Run(Servo_Prg_39_2, Servo_Prg_39_2_Step);
        Servo_PROGRAM_Run(Servo_Prg_39_3, Servo_Prg_39_3_Step);
        Servo_PROGRAM_Center();
        break;
      case 10: // 太極拳動作
        Servo_PROGRAM_Run(Servo_Prg_40, Servo_Prg_40_Step);
        Servo_PROGRAM_Center();
        break;
      case 99:  // 動作 AUTO DEMO
        Servo_PROGRAM_Run(Servo_Prg_32, Servo_Prg_32_Step);
        Servo_PROGRAM_Center();
        delay(500);
        Servo_PROGRAM_Run(Servo_Prg_36, Servo_Prg_36_Step);
        Servo_PROGRAM_Center();
        delay(500);
        Servo_PROGRAM_Run(Servo_Prg_34, Servo_Prg_34_Step);
        Servo_PROGRAM_Center();
        delay(500);
        Servo_PROGRAM_Run(Servo_Prg_35, Servo_Prg_35_Step);
        Servo_PROGRAM_Center();
        delay(500);
        Servo_PROGRAM_Run(Servo_Prg_37, Servo_Prg_37_Step);
        Servo_PROGRAM_Center();
        delay(500);
        Servo_PROGRAM_Run(Servo_Prg_31, Servo_Prg_31_Step);
        Servo_PROGRAM_Center();
        break;
    }
    Servo_PROGRAM_Stack = 0;
  }


  // 電壓偵測
  if (Voltage_Conter >= 30000)
  {
    Voltage = (Voltage + map(analogRead(A0), 0, 1025, 0, Set_Voltage)) / 2;

    char buffer[20];
    itoa(Voltage, buffer, 10);
    if (Input_Voltage_Low == 1 )
    {
      ShowVoltage = "Battery Low !";
    }
    else
    {
      ShowVoltage = "Voltage Value = ";
      ShowVoltage = ShowVoltage + buffer;
    }

    Serial.print("Real VoltageValue = ");
    Serial.print(analogRead(A0));
    if (Input_Voltage_Low == 1 )
    {
      Serial.println(", Calc Value = Battery Low");
    }
    else
    {
      Serial.print(", Calc Value = ");
      Serial.println(Voltage);
    }

    OLED_Display_Index = OLED_Display_Index + 8;
    if (OLED_Display_Index > 56) {
      OLED_Display_Index = 0;
      display.clearDisplay();
    }
    display.setCursor(0, OLED_Display_Index);
    display.print("Voltage Value = ");
    display.println(Voltage);
    display.display();

    // 自動校正電壓誤差
    if (Engineering_Model == 1)
    {
      if (Voltage >= 601) {
        GPIO12SERVO.write(120);

        Voltage_Cab--;
        writeKeyValue(22, Voltage_Cab);
        Set_Voltage = Input_Voltage + Voltage_Cab;
      }
      else if (Voltage <= 599) {
        GPIO12SERVO.write(60);

        Voltage_Cab++;
        writeKeyValue(22, Voltage_Cab);
        Set_Voltage = Input_Voltage + Voltage_Cab;
      }
      else {
        GPIO12SERVO.write(90);
      }
    }
    else
    {
      if (Voltage <= Input_MinVoltage)
      {
        // 低壓禁止動作
        //Input_Voltage_Low = 1;
      }
    }

    Voltage_Conter = 0;
  }
  else {
    Voltage_Conter++;
  }


  // 連接偵測
  if (WiFi.softAPgetStationNum() == 0)
  {
    Serial.println("Disconnect !");

    OLED_Display_Index = OLED_Display_Index + 8;
    if (OLED_Display_Index > 56) {
      OLED_Display_Index = 0;
      display.clearDisplay();
    }
    display.setCursor(0, OLED_Display_Index);
    display.println("Disconnect !");
    display.display();

    while (WiFi.softAPgetStationNum() == 0)
    {
      delay(200);
    }

    Serial.println("");
    Serial.println("Connected !");
  }


}
